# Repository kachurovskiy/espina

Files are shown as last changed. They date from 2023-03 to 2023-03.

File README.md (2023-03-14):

This project is provided "as is", without warranty of any kind ([see license](LICENSE)).

# espina

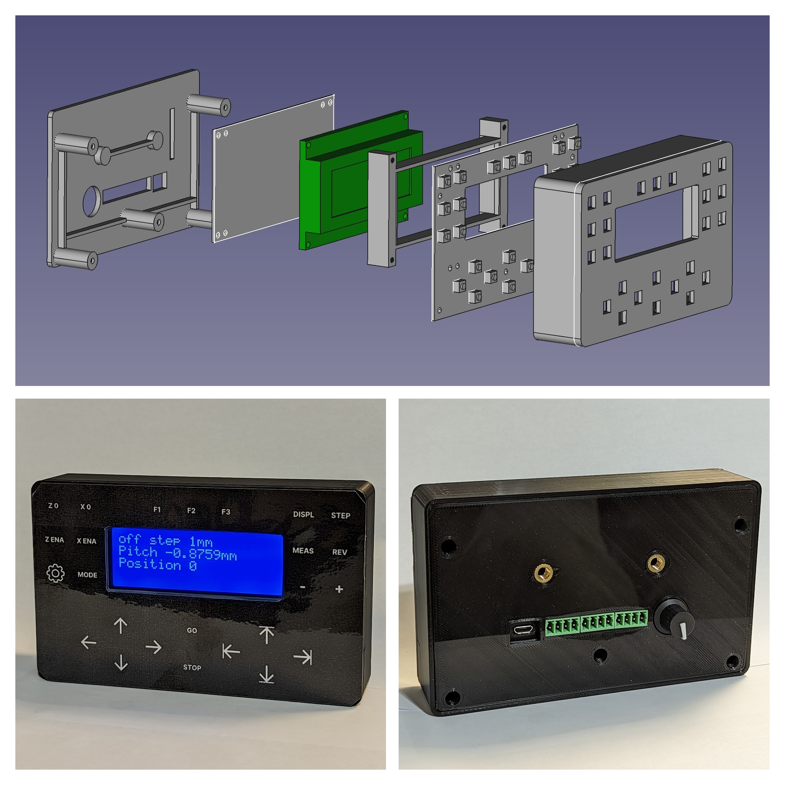
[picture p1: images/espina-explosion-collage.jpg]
Collage


ESP32 controller (PCBs, screen, case) with 1 encoder and 2 steppers. It can be used to control machinery e.g. a metal lathe or a gear cutter. Device can easily be programmed with Arduino or similar IDEs via a USB port.

# Parts

- 2x custom PCBs
- LCD 2004 standard 4-line screen
- [12-pin same-side 1mm pitch FFC connector 5cm](https://www.lcsc.com/product-detail/_JUSHUO-_C2857580.html)
- 4x 3D-printed plastic parts
- 13x M3 bolts
- Optionally, 2x M5 threaded inserts for mounting

# Schematic

espina schematic

# Printed circuit boards

Schematics and PCB layout can be viewed and edited using EasyEDA by copying [projects from `easyeda` folder](https://github.com/kachurovskiy/espina/tree/main/easyeda) to your local computer and opening them in the editor.

Gerber, BOM and pick-and-place files can be found in the [`gerber` folder](https://github.com/kachurovskiy/espina/tree/main/gerber). Smallest production run of these boards on JLCPCB would cost [$200 for 5 boards each](https://user-images.githubusercontent.com/517919/224640478-c27c72a2-1f7f-4686-9f80-fe1553a87b9b.png).

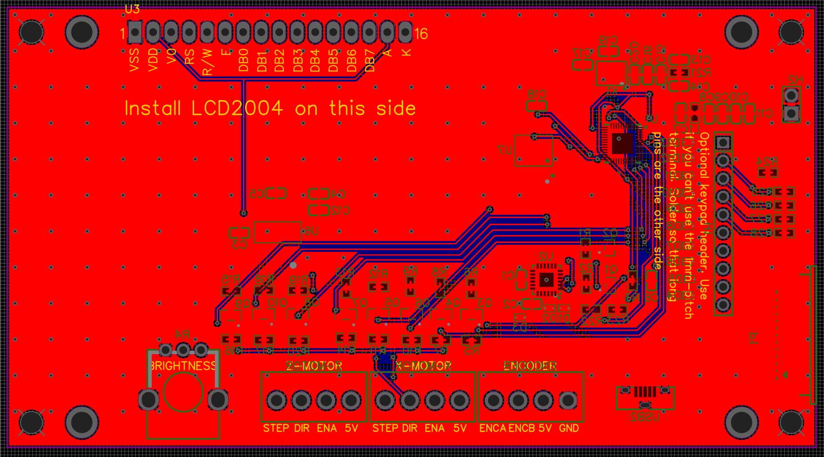
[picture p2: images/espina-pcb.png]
PCB


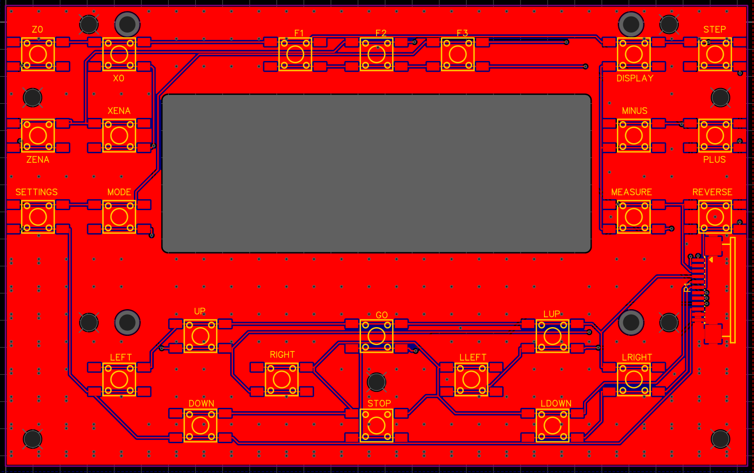
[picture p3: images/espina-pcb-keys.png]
PCB keys


Note: when ordering, JLCPCB sometimes doesn't recognize the FFC terminal part. Use the "Find part" feature, find and select [C14431](https://www.lcsc.com/product-detail/FFC-FPC-Connectors_JUSHUO-AFA07-S12FCC-00_C14431.html). Also, exclude the 2.54 headers from PCBA since you probably don't need them.

# Case

Case is designed to be 3D-printed and [consists of 4 parts](case). It assembles together with 12 M3 bolts, each 5mm long. Galvanized steel bolts are ideal since printed threads are usually too tight for nylon bolts. FreeCAD source file is also provided so it's easy to change models.

# Front panel

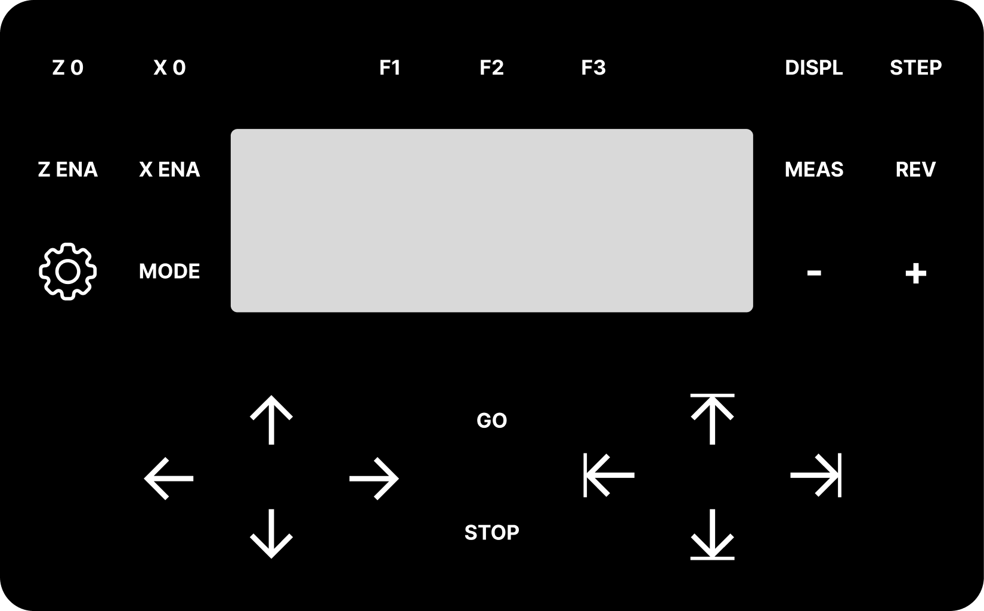
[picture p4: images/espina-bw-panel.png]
Panel Figma


Front panel can be printed on a regular printer from [this PDF](images/espina-bw-panel.pdf) with 90% scale, window cut out with a knife and then laminated. [Medium thickness double-sided tape is applied](https://i.imgur.com/JJHeC12.jpg) on the case around buttons and front panel is glued to it.

If you want to design your own panel, you can start by editing [this file](images/espina-bw-panel.fig) on [figma.com](https://www.figma.com/) for free.

# Software

One sample program for this controller is a single-axis electronic lead screw for a metal lathe, see [espinaels](https://github.com/kachurovskiy/espina/tree/main/espinaels) folder.

# Project status

This project "archived" - I decided to completely re-design it so making this historical version available for free. Drawbacks of the current design are suboptimal LCD viewing angles, older ESP32 version, lack of ESD protection, only 2 axes, old-style USB port. This version of the ELS software might not be developed much further.

# Contributions

Please report any bugs or problems. For changes and improvements, consider forking the repository and developing in parallel.

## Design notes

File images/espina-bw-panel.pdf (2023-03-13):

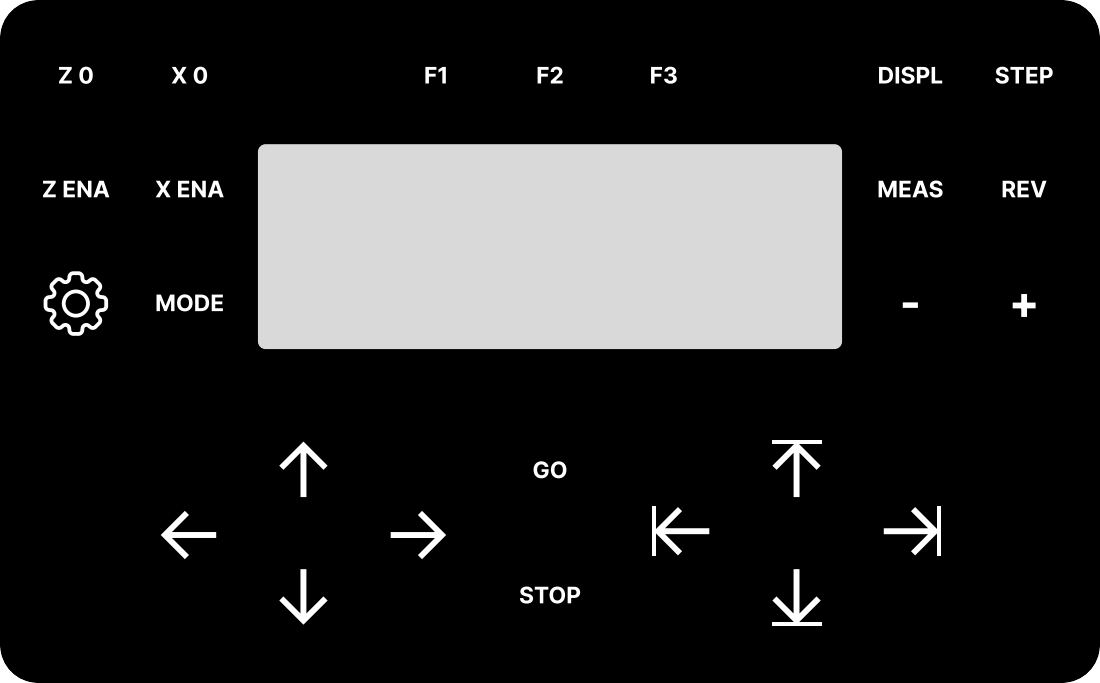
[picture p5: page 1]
STOP; DISPL; MODE; STEP; MEAS; REV; Z ENA; X ENA

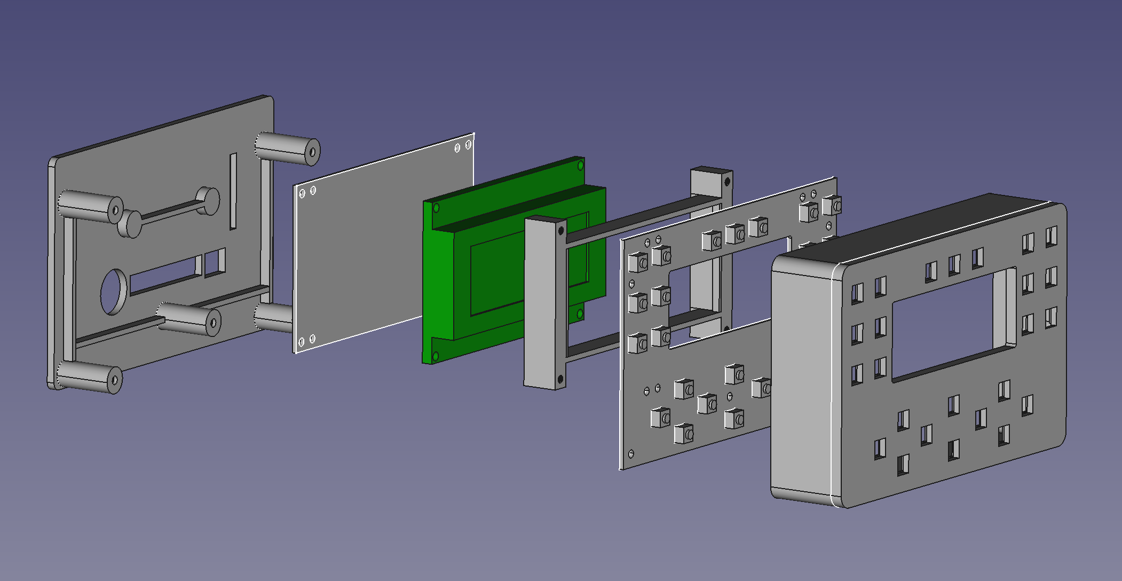
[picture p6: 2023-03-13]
images/espina-explosion.png

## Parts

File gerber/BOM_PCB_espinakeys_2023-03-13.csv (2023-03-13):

ID | Name | Designator | Footprint | Quantity | Manufacturer Part | Manufacturer | Supplier | Supplier Part | Price | Pins | 3DModel | Contributor | link
1 | KH-6X6X5H-STM | DISPLAY,DOWN,F1,F2,F3,GO,LDOWN,LEFT,LLEFT,LRIGHT,LUP,MEASURE,MINUS,MODE,PLUS,REVERSE,RIGHT,SETTINGS,STEP,STOP,UP,X0,XENA,Z0,ZENA | SW-SMD_4P-L6.0-W6.0-P4.50-LS9.0-2 | 25 | KH-6X6X5H-STM | kinghelm(金航标) | LCSC | C2837531 | 0.003 | 4 | SW-SMD_4P-L6.0-W6.0-P4.50-LS11.0 | LCSC | https://so.szlcsc.com/global.html?c=&k=C620319
2 | FPCConnector Pull type 12PIN 1MM Under the next | P1 | FPC-SMD_AFA07-S12FCC-00 | 1 | AFA07-S12FCC-00 | JS(钜硕电子) | LCSC | C14431 | 0.015 | 14 | FPC-SMD_L19.0-W6.9-H2.5-AFA07-S12FCC-00 | 立创EDA官方封装库 | https://item.szlcsc.com/15091.html

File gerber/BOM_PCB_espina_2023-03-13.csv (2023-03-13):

ID | Name | Designator | Footprint | Quantity | Manufacturer Part | Manufacturer | Supplier | Supplier Part | Price | Pins | 3DModel | Contributor | Frequency | Resistance | Resistance (Ohms) | link
1 | LCD2004 | U3 | LCD2004-PHT | 1 |  |  |  |  |  | 20 |  | Tomaž Dežman
2 | DB2EVC-3.5-4P-GN | ENCODER,X-MOTOR,Z-MOTOR | CONN-TH_4P-P3.50_DB2EVC-3.5-4P-GN | 3 | DB2EVC-3.5-4P-GN | DIBO(地博电气) | LCSC | C430552 | 0.016 | 4 | CONN-TH_4P-P3.50_DB2EVC-3.5-4P-GN | LCSC |  |  |  | https://item.szlcsc.com/426197.html
3 | KH-2.54PH180-1X2P-L11.5 | H2 | HDR-TH_2P-P2.54-V-M | 1 | KH-2.54PH180-1X2P-L11.5 | kinghelm(金航标) | LCSC | C2905434 | 0.003 | 2 | HDR2.54-M-LI-1X2P | LCSC |  |  |  | https://lcsc.com/product-detail/Pin-Header-Female-Header_Made-in-China-Made-in-China-2-54mm-1-2P_C36717.html
4 | SI2302ADS-T1 | Q7,Q6,Q4,Q3,Q5,Q8,Q9,Q10 | SOT-23-3_L2.9-W1.3-P1.90-LS2.4-BR | 8 | SI2302ADS-T1-VB | VBsemi(微碧) | LCSC | C725156 | 0.012 | 3 | SOT-23-3P_L2.9-W1.3-H1.0-LS2.4-P0.95 | LCSC |  |  |  | https://www.diodes.com/assets/Package-Files/SOT23.pdf
5 | 2kΩ | R7,R8,R6,R5,R13,R14,R10,R9,R11,R12,R15,R16,R17,R18,R19,R20,R24,R25,R26,R27,R28 | R0603 | 21 | RMC06032K1%N | Tyohm(幸亚电阻) | LCSC | C269421 | 0.001 | 2 | R0603_L1.6-W0.8-H0.8 | LCSC |  |  | 2K | https://www.mouser.in/datasheet/2/447/PYu_RT_1_to_0_01_RoHS_L_11-1669912.pdf
6 | KH-2.54PH180-1X10P-L11.5 | H1 | HDR-TH_10P-P2.54-V-M | 1 | KH-2.54PH180-1X10P-L11.5 | kinghelm(金航标) | LCSC | C2905488 | 0.015 | 10 | HDR2.54-M-LI-1X10P | LCSC |  |  |  | https://item.szlcsc.com/502965.html
7 | 100nF | C2,C5,C7,C17,C12,C8 | C0603 | 6 | C0603C104J5RAC | KEMET | LCSC | C490602 | 0.002 | 2 | C0603_L1.6-W0.8-H0.8 | LCSC |  |  |  | https://item.szlcsc.com/362304.html
8 | S9013W | Q1,Q2 | SOT-323-3_L2.0-W1.3-P1.30-LS2.1-BR | 2 | S9013W | CJ(江苏长电/长晶) | LCSC | C37634 | 0.005 | 3 | SOT-323-3_L2.0-W1.3-H1.0-LS2.1-P1.30 | lcsc |  |  |  | https://item.szlcsc.com/76687.html
9 | AMS1117-3.3 | U6 | SOT-223-3_L6.4-W3.5-P2.30-LS7.0-BR | 1 | AMS1117-3.3 | 国芯佳品 | LCSC | C2992570 | 0.008 | 4 | SOT-223-3_L6.4-W3.5-P2.30-LS7.0-BR | lcsc |  |  |  | https://atta.szlcsc.comnull
10 | ULC0511CDN | D1,D2,D3,D4,D5,D6,D7,D8,D9,D10,D11,D12,D13 | X1-DFN1006-2_L1.0-W0.6-RD | 13 | ULC0511CDN | Leiditech(雷卯电子) | LCSC | C384841 | 0.008 | 2 | DFN1006_L1.0-W0.6-H0.5 | LCSC |  |  |  | https://item.szlcsc.com/162710.html
11 | 40MHz | X1 | OSC-SMD_4P-L3.2-W2.5-BL_SIT8008BI | 1 | X322540MPB4SI | YXC(扬兴晶振) | LCSC | C9010 | 0.015 | 4 | OSC-SMD_4P-L3.2-W2.5-H1.0 | lcsc |  |  |  | https://item.szlcsc.com/264073.html
12 | 10nF | C13 | C0603 | 1 | CC0603KRX7R9BB103 | YAGEO(国巨) | LCSC | C100042 |  | 2 | C0603_L1.6-W0.8-H0.8 | lcsc |  |  |  | https://item.szlcsc.com/362304.html
13 | 3.3nF | C14 | C0603 | 1 | CC0603KRX7R7BB332 | YAGEO | LCSC | C519418 | 0.001 | 2 | C0603_L1.6-W0.8-H0.8 | LCSC |  |  |  | https://item.szlcsc.com/362304.html
14 | 100pF | C15 | C0603 | 1 | CC0603KRX7R9BB101 | YAGEO(国巨) | LCSC | C160903 |  | 2 | C0603_L1.6-W0.8-H0.8 | LCSC |  |  |  | https://item.szlcsc.com/362304.html
15 | 2nH | L1 | L0603 | 1 | SDCL1608C2N0STDF | Sunlord | LCSC | C370234 | 0.001 | 2 | L0603_L1.6-W0.8-H0.5_BEAD | LCSC |  |  |  | https://item.szlcsc.com/344093.html
16 | 20K | R21 | R0603 | 1 | AC0603FR-0720KL | YAGEO(国巨) | LCSC | C125934 |  | 2 | R0603_L1.6-W0.8-H0.8 | lcsc |  | 20kΩ |  | https://www.mouser.in/datasheet/2/447/PYu_RT_1_to_0_01_RoHS_L_11-1669912.pdf
17 | ESP32-D0WD | U1 | QFN-48_L5.0-W5.0-P0.35-BL-EP3.7 | 1 | ESP32-D0WD | ESPRESSIF(乐鑫) | LCSC | C130167 | 0.344 | 49 | QFN-48_L5.0-W5.0-H0.9-P0.35-BL-EP3.7 | LCSC | - |  |  | https://item.szlcsc.com/479661.html
18 | W25Q32JVSSIQ | U7 | SOIC-8_L5.3-W5.3-P1.27-LS8.0-BL | 1 | W25Q32JVSSIQ | WINBOND(华邦) | LCSC | C179173 | 0.052 | 8 | SOIC-8_L5.3-W5.3-H1.9-LS7.9-P1.27 | LCSC |  |  |  | https://item.szlcsc.com/63461.html
19 | 1uF | C1,C6,C10,C16,C18 | C0603 | 5 | 0603B105K160AT | FH(风华) | LCSC | C111770 | 0.002 | 2 | C0603_L1.6-W0.8-H0.8 | lcsc |  |  |  | https://item.szlcsc.com/362304.html
20 | 10uF | C3,C4,C9,C11 | C0603 | 4 | 0603X106K160NT | FH(风华) | LCSC | C70225 | 0.007 | 2 | C0603_L1.6-W0.8-H0.8 | lcsc |  |  |  | https://item.szlcsc.com/362304.html
21 | 15pF | C19,C20 | C0603 | 2 | CC0603JRNPO9BN150 | YAGEO(国巨) | LCSC | C107037 |  | 2 | C0603_L1.6-W0.8-H0.8 | lcsc |  |  |  | https://item.szlcsc.com/362304.html
22 | 10kΩ | R1,R2,R3 | R0603 | 3 | RMC060310KFN | Tyohm(幸亚电阻) | LCSC | C269701 | 0.001 | 2 | R0603_L1.6-W0.8-H0.8 | LCSC |  |  | 10K | https://www.mouser.in/datasheet/2/447/PYu_RT_1_to_0_01_RoHS_L_11-1669912.pdf
23 | 470 | R22,R23 | R0603 | 2 | RC0603JR-07470RL | YAGEO(国巨) | LCSC | C114433 |  | 2 | R0603_L1.6-W0.8-H0.8 | lcsc |  | 470Ω |  | https://www.mouser.in/datasheet/2/447/PYu_RT_1_to_0_01_RoHS_L_11-1669912.pdf
24 | CH9102F | U2 | QFN-24_L4.0-W4.0-P0.50-BL-EP2.5 | 1 | CH9102F | WCH(南京沁恒) | LCSC | C2858418 | 0.221 | 25 | QFN-24_L4.0-W4.0-P0.50-BL-EP2.5 | LCSC |  |  |  | http://ww1.microchip.com/downloads/en/DeviceDoc/00002165B.pdf
25 | 10kΩ | R4 | RES-ADJ-TH_RK09K1130AJ3 | 1 | RK09K1130AJ3 | ALPSALPINE(阿尔卑斯阿尔派) | LCSC | C388854 | 0.099 | 5 | RES-ADJ-TH_RK09K1130AJ3 | LCSC |  |  |  | https://lcsc.com/product-detail/New-Arrivals_ALPS-Electric-RK09K1130AJ3_C388854.html
26 | 1051330011 | USB2 | MICRO-USB-SMD_1051330011 | 1 | 1051330011 | MOLEX | LCSC | C586226 | 0.069 | 8 | MICRO-USB-SMD_1051330011 | LCSC |  |  |  | https://item.szlcsc.com/614076.html?ref=editor&logined=true
27 | FPCConnector Pull type 12PIN 1MM Under the next | P1 | FPC-SMD_AFA07-S12FCC-00 | 1 | AFA07-S12FCC-00 | JS(钜硕电子) | LCSC | C14431 | 0.015 | 14 | FPC-SMD_L19.0-W6.9-H2.5-AFA07-S12FCC-00 | 立创EDA官方封装库 |  |  |  | https://item.szlcsc.com/15091.html

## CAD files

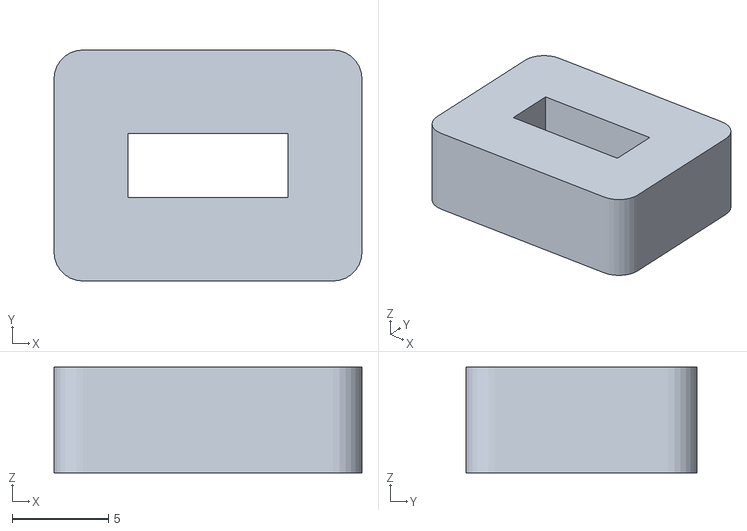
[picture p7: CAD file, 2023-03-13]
case/espina-USB collar.stl
16.0 x 12.0 x 5.50

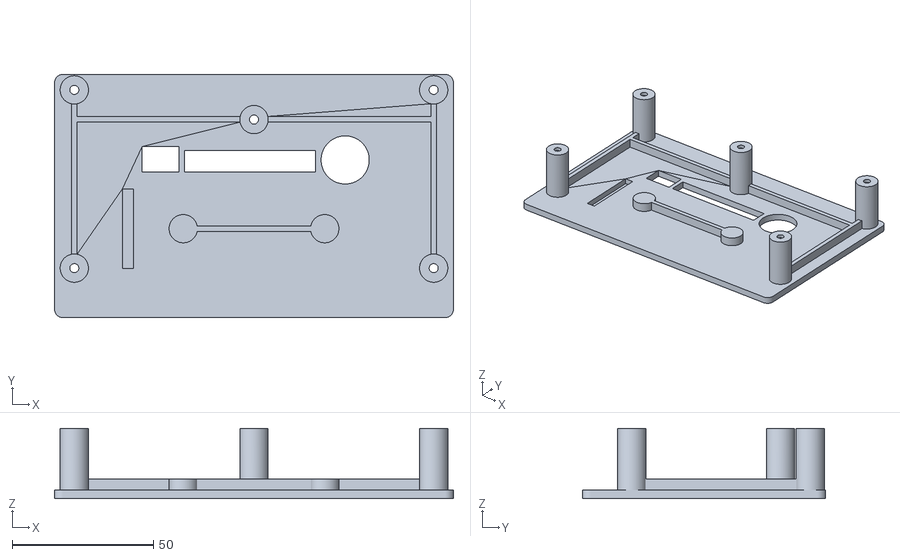
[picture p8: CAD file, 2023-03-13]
case/espina-Back.stl
141.0 x 86.0 x 24.9

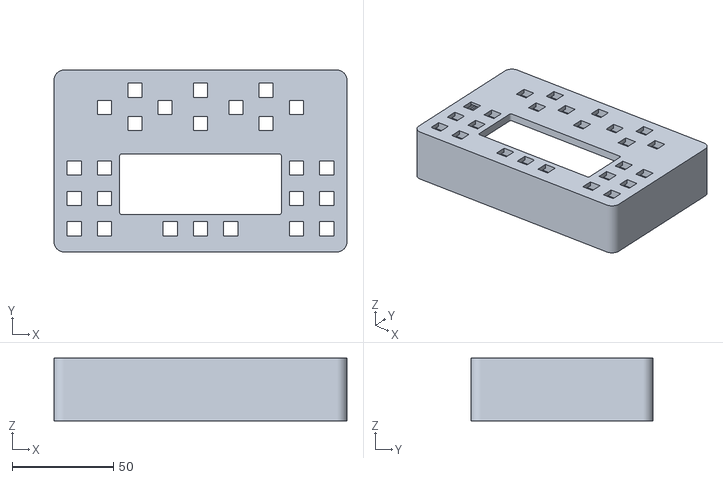
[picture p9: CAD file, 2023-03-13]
case/espina-Case.stl
145.0 x 90.0 x 31.0

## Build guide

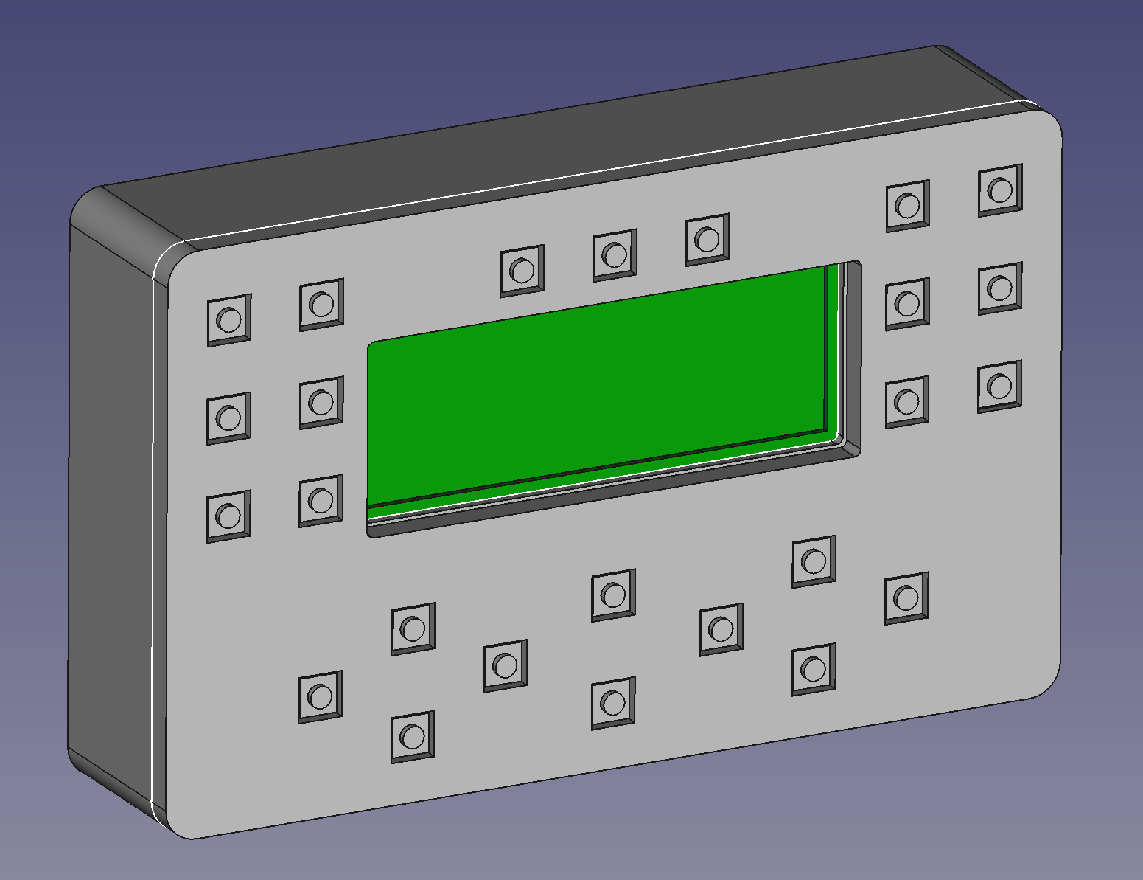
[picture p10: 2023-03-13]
images/espina-assembled.png

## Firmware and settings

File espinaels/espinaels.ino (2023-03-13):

// https://github.com/kachurovskiy/espina

/* Change values in this section to suit your hardware. */

// Define your hardware parameters here. Don't remove the ".0" at the end.
#define ENCODER_STEPS 600.0 // 600 step spindle optical rotary encoder
#define MOTOR_STEPS 200.0
#define LEAD_SCREW_DU 20000.0 // 2mm lead screw in deci-microns (10^-7) of a meter

// Spindle rotary encoder pins. Swap values if the rotation direction is wrong.
#define ENC_A 36
#define ENC_B 39

// Stepper pulse and acceleration constants.
#define PULSE_MIN_US round(500.0 * 200.0 / MOTOR_STEPS) // Microseconds to wait after high pulse, min.
#define PULSE_MAX_US round(2000.0 * 200.0 / MOTOR_STEPS) // Microseconds to wait after high pulse, max. Slow start.
#define ACCELERATION 20
#define INVERT_STEPPER false // change (true/false) if the carriage moves e.g. "left" when you press "right".
#define DISABLE_STEPPER_WHEN_RESTING false

/* Changing anything below shouldn't be needed for basic use. */

#define LONG_MIN long(-2147483648)
#define LONG_MAX long(2147483647)

#define LOOP_COUNTER_MAX 1500 // 1500 loops without stepper move to start reading buttons
#define DUPR_MAX long(100000) // 10mm
#define STARTS_MAX 124 // No more than 124-start thread

// Ratios between spindle and stepper.
#define ENCODER_TO_STEPPER_STEP_RATIO MOTOR_STEPS / (LEAD_SCREW_DU * ENCODER_STEPS)
#define STEPPER_TO_ENCODER_STEP_RATIO LEAD_SCREW_DU * ENCODER_STEPS / MOTOR_STEPS

// If time between encoder ticks is less than this, direction change is not allowed.
// Effectively this limits direction change to the time when spindle is <20rpm.
#define DIR_CHANGE_DIFF_MICROS (int) (5000 * ENCODER_STEPS / 600)

// Version of the EEPROM storage format, should be changed when non-backward-compatible
// changes are made to the storage logic, resulting in EEPROM wipe on first start.
#define EEPROM_VERSION 1

// To be incremented whenever a measurable improvement is made.
#define SOFTWARE_VERSION 1

// To be changed whenever a different PCB / encoder / stepper / ... design is used.
#define HARDWARE_VERSION 1

#define Z_DIR 16
#define Z_STEP 17
#define Z_ENA 4

#define X_DIR 26
#define X_STEP 25
#define X_ENA 27

// Keypad columns left-to-right
#define KP_1 34 // input only, no pull-up/down
#define KP_2 35 // input only, no pull-up/down
#define KP_3 32
#define KP_4 33
#define KP_5 14

// Keypad rows bottom-to-top
#define KP_6 12
#define KP_7 13
#define KP_8 15
#define KP_9 2
#define KP_10 0

// Code for each button calculated as row*100+column
#define B_LEFT  33
#define B_RIGHT 214
#define B_MINUS 1332
#define B_PLUS 1232
#define B_ON 1533
#define B_OFF 1514
#define B_STOPL 1314
#define B_STOPR 1233
#define B_DISPL 1334
#define B_STEP 1234
#define B_MODE 232
#define B_MEASURE 1335
#define B_REVERSE 1235

#define ADDR_EEPROM_VERSION 0 // takes 1 byte
#define ADDR_ONOFF 1 // takes 1 byte
#define ADDR_DUPR 2 // takes 4 bytes
#define ADDR_POS 6 // takes 4 bytes
#define ADDR_LEFT_STOP 10 // takes 4 bytes
#define ADDR_RIGHT_STOP 14 // takes 4 bytes
#define ADDR_SPINDLE_POS 18 // takes 4 bytes
#define ADDR_OUT_OF_SYNC 22 // takes 2 bytes
#define ADDR_SHOW_ANGLE 24 // takes 1 byte
#define ADDR_SHOW_TACHO 25 // takes 1 byte
#define ADDR_MOVE_STEP 26 // takes 2 bytes
#define ADDR_STARTS 28 // takes 2 bytes
#define ADDR_MODE 30 // takes 2 bytes
#define ADDR_MEASURE 32 // takes 2 bytes

#define MOVE_STEP_1 10000 // 1mm
#define MOVE_STEP_2 1000 // 0.1mm
#define MOVE_STEP_3 100 // 0.01mm
#define MOVE_STEP_4 10 // 1 micron
#define MOVE_STEP_IMP_1 25400 // 1/10"
#define MOVE_STEP_IMP_2 2540 // 1/100"
#define MOVE_STEP_IMP_3 254 // 1/1000" also known as 1 thou

#define MODE_NORMAL 0
#define MODE_MULTISTART 1
#define MODE_ASYNC 2

#define MEASURE_METRIC 0
#define MEASURE_INCH 1
#define MEASURE_TPI 2

// For MEASURE_TPI, round TPI to the nearest integer if it's within this range of it.
// E.g. 80.02tpi would be shown as 80tpi but 80.04tpi would be shown as-is.
#define TPI_ROUND_EPSILON 0.03

#define RPM_BULK ENCODER_STEPS // Measure RPM averaged over this number of encoder pulses
#define RPM_UPDATE_INTERVAL_MICROS 1000000 // Don't redraw RPM more often than once per second

// Uncomment to print out debug info in Serial.
// #define DEBUG

#define DREAD(x) digitalRead(x)
#define DHIGH(x) digitalWrite(x, HIGH)
#define DLOW(x) digitalWrite(x, LOW)

#include <SPI.h>
#include <Wire.h>
#include <LiquidCrystal.h>
LiquidCrystal lcd(5, 18, 23, 19, 22, 21);
long lcdHash = 0;

#include <EEPROM.h>

unsigned long buttonDownTime = 0;
unsigned long buttonUpTime = 0;
int buttonId = 0;
volatile long loopCounter = 0;
int buttonLoopCounter = 0;
bool isOn = false;
unsigned long resetMillis = 0;
bool resetOnStartup = false;

volatile long dupr = 0; // pitch, tenth of a micron per rotation
long savedDupr = 0; // dupr saved in EEPROM
long duprPrevious = 0;

int starts = 1; // number of starts in a multi-start thread
int savedStarts = 0; // starts saved in EEPROM

volatile long pos = 0; // relative position of the stepper motor, in steps
long savedPos = 0; // value saved in EEPROM
float fractionalPos = 0.0; // fractional distance in steps that we meant to travel but couldn't

volatile long leftStop = 0; // left stop value of pos
long savedLeftStop = 0; // value saved in EEPROM
bool leftStopFlag = true; // prevent toggling the stop while button is pressed.

volatile long rightStop = 0; // right stop value of pos
long savedRightStop = 0; // value saved in EEPROM
bool rightStopFlag = true; // prevent toggling the stop while button is pressed.

volatile unsigned long spindleEncTime = 0; // micros() of the previous spindle update
volatile unsigned long spindleEncTimeDiff = 0; // micros() since the previous spindle update
volatile unsigned long spindleEncTimeDiffBulk = 0; // micros() between RPM_BULK spindle updates
volatile unsigned long spindleEncTimeAtIndex0 = 0; // micros() when spindleEncTimeIndex was 0
volatile int spindleEncTimeIndex = 0; // counter going between 0 and RPM_BULK - 1
volatile int spindleDeltaPrev = 0; // Previously detected spindle direction
volatile long spindlePos = 0; // Spindle position
long savedSpindlePos = 0; // spindlePos value saved in EEPROM
long spindleLeftStop = 0;
long spindleRightStop = 0;

volatile int spindlePosSync = 0;
int savedSpindlePosSync = 0;

volatile int stepDelayUs = PULSE_MAX_US;
volatile bool stepDelayDirection = true; // To reset stepDelayUs when direction changes.
volatile bool stepDirectionInitialized = false;
volatile unsigned long stepStartMicros = 0;
int stepperEnableCounter = 0;

bool showAngle = false; // Whether to show 0-359 spindle angle on screen
bool showTacho = false; // Whether to show spindle RPM on screen
bool savedShowAngle = false; // showAngle value saved in EEPROM
bool savedShowTacho = false; // showTacho value saved in EEPROM
int shownRpm = 0;
unsigned long shownRpmTime = 0; // micros() when shownRpm was set

int moveStep = 0; // thousandth of a mm
int savedMoveStep = 0; // moveStep saved in EEPROM
volatile bool movingManually = false; // whether stepper is being moved by left/right buttons

volatile int mode = -1; // mode of operation (ELS, multi-start ELS, asynchronous)
int savedMode = -1; // mode saved in EEPROM

int measure = MEASURE_METRIC; // Whether to show distances in inches
int savedMeasure = MEASURE_METRIC; // measure value saved in EEPROM

int getApproxRpm() {
  if (!showTacho) {
    return 0;
  }
  unsigned long t = micros();
  if (t > spindleEncTime + 100000) {
    // RPM less than 10.
    return 0;
  }
  if (t < shownRpmTime + RPM_UPDATE_INTERVAL_MICROS) {
    // Don't update RPM too often to avoid flickering.
    return shownRpm;
  }
  int rpm = 0;
  if (spindleEncTimeDiffBulk > 0) {
    rpm = 60000000 / spindleEncTimeDiffBulk;
    if (abs(rpm - shownRpm) < (rpm < 1000 ? 2 : 5)) {
      // Don't update RPM with insignificant differences.
      rpm = shownRpm;
    }
  }
  return rpm;
}

bool stepperIsRunning() {
  return micros() - stepStartMicros < 10000;
}

void printMicrons(long deciMicrons) {
  if (deciMicrons == 0) {
    lcd.print("0");
    return;
  }
  bool imperial = measure != MEASURE_METRIC;
  long v = imperial ? round(deciMicrons / 25.4) : deciMicrons;
  int points = 0;
  if (v == 0) {
    points = 5;
  } else if ((v % 10) != 0) {
    points = 4;
  } else if ((v % 100) != 0) {
    points = 3;
  } else if ((v % 1000) != 0) {
    points = 2;
  } else if ((v % 10000) != 0) {
    points = 1;
  }
  lcd.print(deciMicrons / (imperial ? 254000.0 : 10000.0), points);
  lcd.print(imperial ? "\"" : "mm");
}

void updateDisplay(bool beforeRunning) {
  int rpm = getApproxRpm();
  // Hide rows 3 and 4 if ON and about to or is already moving.
  // Not hiding when off since it results in flickering of rows 3 and 4 during short manual moves.
  bool running = isOn && (beforeRunning || stepperIsRunning());
  // Sum of values affecting rows 1 and 2 of the LCD.
  long hashRows12 = dupr + isOn * 2 + leftStop / 3
                    + rightStop / 4 + spindlePosSync * 5 + resetOnStartup * 6
                    + moveStep * 7 + running * 8 + starts * 12 + mode * 13 + measure * 14;
  // Sum of values affecting rows 3 and 4 of the LCD.
  long hashRows34 = pos * 9 + showAngle * 10 + (showTacho ? rpm : -1) * 11 + measure * 14;
  // Ignore changes in hashRows34 when stepper is running since they aren't shown.
  long newLcdHash = hashRows12 + (running ? 0 : hashRows34);
  // Don't show angle if stepper is running or spindle is turning.
  bool spindleStopped = micros() > spindleEncTime + 100000;
  if (!running && showAngle && spindleStopped) {
    newLcdHash += spindlePos;
  }

  // Don't spend 40ms and flicker the screen if nothing changed.
  if (newLcdHash == lcdHash) {
    return;
  }

  lcdHash = newLcdHash;
  lcd.clear();

  // First row.
  lcd.setCursor(0, 0);
  if (mode == MODE_MULTISTART) {
    lcd.print("MUL ");
  } else if (mode == MODE_ASYNC) {
    lcd.print("ASY ");
  }
  lcd.print(isOn ? "ON" : "off");
  if (leftStop != LONG_MAX && rightStop != LONG_MIN) {
    lcd.print(" LR");
  } else if (leftStop != LONG_MAX) {
    lcd.print(" L");
  } else if (rightStop != LONG_MIN) {
    lcd.print("  R");
  }

  if (spindlePosSync) {
    lcd.print(" SYN");
  }
  if (resetOnStartup) {
    lcd.print(" LTW");
  }
  if (mode == MODE_NORMAL && !resetOnStartup && !spindlePosSync) {
    lcd.print(" step ");
  } else {
    lcd.print(" ");
  }
  printMicrons(moveStep);

  // Second row.
  lcd.setCursor(0, 1);
  lcd.print("Pitch ");
  if (measure != MEASURE_TPI) {
    printMicrons(dupr);
  } else {
    float tpi = 254000.0 / dupr;
    if (abs(tpi - round(tpi)) < TPI_ROUND_EPSILON) {
      lcd.print(round(tpi));
    } else {
      int tpi100 = round(tpi * 100);
      int points = 0;
      if ((tpi100 % 10) != 0) {
        points = 2;
      } else if ((tpi100 % 100) != 0) {
        points = 1;
      }
      lcd.print(tpi, points);
    }
    lcd.print("tpi");
  }
  if (starts != 1) {
    lcd.print(" x");
    lcd.print(starts);
  }

  if (running) {
    // Stepper is running, updateDisplay() will no longer be called soon,
    // don't draw position, RPM and angle that won't be accurate shortly.
    return;
  }

  // Third row.
  lcd.setCursor(0, 2);
  lcd.print("Position ");
  printMicrons(round(pos * LEAD_SCREW_DU / MOTOR_STEPS));

  // Fourth row.
  lcd.setCursor(0, 3);
  if (showAngle) {
    lcd.print("Angle ");
    if (spindleStopped) {
      lcd.print(((spindlePos % (int) ENCODER_STEPS + (int) ENCODER_STEPS) % (int) ENCODER_STEPS) * 360 / ENCODER_STEPS, 2);
      lcd.print(char(223));
    }
  } else if (showTacho) {
    lcd.print("Tacho ");
    lcd.print(rpm);
    if (shownRpm != rpm) {
      shownRpm = rpm;
      shownRpmTime = micros();
    }
    lcd.print("rpm");
  }
}

void saveInt(int i, int v) {
  // Can't concatenate all in one line due to compiler problems, same throughout the code.
#ifdef DEBUG
  Serial.print("Saving int at ");
  Serial.print(i);
  Serial.print(" = ");
  Serial.println(v);
#endif
  EEPROM.write(i, v >> 8 & 0xFF);
  EEPROM.write(i + 1, v & 0xFF);
}
int loadInt(int i) {
  // 255 is the default value when nothing was written before.
  if (EEPROM.read(i) == 255 && EEPROM.read(i + 1) == 255) {
    return 0;
  }
  return (EEPROM.read(i) << 8) + EEPROM.read(i + 1);
}
void saveLong(int i, long v) {
#ifdef DEBUG
  Serial.print("Saving long at ");
  Serial.print(i);
  Serial.print(" = ");
  Serial.println(v);
#endif
  EEPROM.write(i, v >> 24 & 0xFF);
  EEPROM.write(i + 1, v >> 16 & 0xFF);
  EEPROM.write(i + 2, v >> 8 & 0xFF);
  EEPROM.write(i + 3, v & 0xFF);
}
long loadLong(int i) {
  long p0 = EEPROM.read(i);
  long p1 = EEPROM.read(i + 1);
  long p2 = EEPROM.read(i + 2);
  long p3 = EEPROM.read(i + 3);
  // 255 is the default value when nothing was written before.
  if (p0 == 255 && p1 == 255 && p2 == 255 && p3 == 255) {
    return 0;
  }
  return (p0 << 24) + (p1 << 16) + (p2 << 8) + p3;
}

// Called on a FALLING interrupt for the spindle rotary encoder pin.
// Keeps track of the spindle position.
void spinEnc() {
  unsigned long microsNow = micros();
  if (spindleEncTimeIndex == 0) {
    spindleEncTimeDiffBulk = microsNow - spindleEncTimeAtIndex0;
    spindleEncTimeAtIndex0 = microsNow;
  }
  spindleEncTimeIndex = (spindleEncTimeIndex + 1) % int(RPM_BULK);

  int delta;
  spindleEncTimeDiff = microsNow - spindleEncTime;
  if (spindleEncTimeDiff > DIR_CHANGE_DIFF_MICROS || !stepDirectionInitialized) {
    delta = DREAD(ENC_B) ? -1 : 1;
    spindleDeltaPrev = delta;
  } else {
    // Spindle is going fast, unlikely to change direction momentarily.
    delta = spindleDeltaPrev;
  }
  spindlePos += delta;
  spindleEncTime = microsNow;

  if (spindlePosSync != 0) {
    spindlePosSync += delta;
    if (spindlePosSync == 0 || spindlePosSync == ENCODER_STEPS) {
      spindlePosSync = 0;
      spindlePos = spindleFromPos(pos);
    }
  }
}

void setup() 
{
  pinMode(ENC_A, INPUT_PULLUP);
  pinMode(ENC_B, INPUT_PULLUP);

  pinMode(Z_DIR, OUTPUT);
  pinMode(Z_STEP, OUTPUT);
  pinMode(Z_ENA, OUTPUT);
  DHIGH(Z_STEP);

  pinMode(X_DIR, OUTPUT);
  pinMode(X_STEP, OUTPUT);
  pinMode(X_ENA, OUTPUT);
  DHIGH(X_STEP);

  EEPROM.begin(256);
  // Wipe EEPROM if this is the first start after uploading a new build.
  if (EEPROM.read(ADDR_EEPROM_VERSION) != EEPROM_VERSION) {
    for (int i = 0; i < 256; i++) {
      EEPROM.write(i, 255); // 255 is the default value.
    }
    EEPROM.write(ADDR_EEPROM_VERSION, EEPROM_VERSION);
    saveLong(ADDR_LEFT_STOP, savedLeftStop = leftStop = LONG_MAX);
    saveLong(ADDR_RIGHT_STOP, savedRightStop = rightStop = LONG_MIN);
    saveInt(ADDR_MOVE_STEP, MOVE_STEP_1);
  }

  isOn = EEPROM.read(ADDR_ONOFF) == 1;
  savedDupr = dupr = loadLong(ADDR_DUPR);
  savedStarts = starts = min(STARTS_MAX, max(1, loadInt(ADDR_STARTS)));
  savedPos = pos = loadLong(ADDR_POS);
  savedLeftStop = leftStop = loadLong(ADDR_LEFT_STOP);
  savedRightStop = rightStop = loadLong(ADDR_RIGHT_STOP);
  savedSpindlePos = spindlePos = loadLong(ADDR_SPINDLE_POS);
  savedSpindlePosSync = spindlePosSync = loadInt(ADDR_OUT_OF_SYNC);
  savedShowAngle = showAngle = EEPROM.read(ADDR_SHOW_ANGLE) == 1;
  savedShowTacho = showTacho = EEPROM.read(ADDR_SHOW_TACHO) == 1;
  savedMoveStep = moveStep = loadInt(ADDR_MOVE_STEP);
  savedMode = loadInt(ADDR_MODE);
  savedMeasure = measure = loadInt(ADDR_MEASURE);
  // Don't move on power-on.
  setMode((isOn && savedMode == MODE_ASYNC) ? MODE_NORMAL : savedMode);

  if (DISABLE_STEPPER_WHEN_RESTING) {
    stepperEnable(isOn);
  } else {
    DHIGH(Z_ENA);
  }

  lcd.begin(20, 4);
  updateDisplay(false /*beforeRunning*/);

  Serial.begin(9600);
  Serial.print("Espina H");
  Serial.print(HARDWARE_VERSION);
  Serial.print(" V");
  Serial.println(SOFTWARE_VERSION);

  preventMoveOnStart();

  attachInterrupt(digitalPinToInterrupt(ENC_A), spinEnc, FALLING);
  
  pinMode(KP_1, INPUT); // no built-in pull-down/up
  pinMode(KP_2, INPUT); // no built-in pull-down/up
  pinMode(KP_3, INPUT_PULLDOWN);
  pinMode(KP_4, INPUT_PULLDOWN);
  pinMode(KP_5, INPUT_PULLDOWN);
  pinMode(KP_6, OUTPUT);
  pinMode(KP_7, OUTPUT);
  pinMode(KP_8, OUTPUT);
  pinMode(KP_9, OUTPUT);
  pinMode(KP_10, OUTPUT);
}

void preventMoveOnStart() {
  // Sometimes, especially if ELS was run outside above max RPM before, pos and spindlePos
  // will be out of sync causing immediate stepper movement if isOn. This could be dangerous
  // and surely won't be expected by the operator.
  long newPos = posFromSpindle(spindlePos, true);
  if (isOn && newPos != pos) {
#ifdef DEBUG
    Serial.println("Losing the thread");
#endif
    resetOnStartup = true;
    markAsZero();
  }
}

// Saves all positions in EEPROM, should be called infrequently to reduce EEPROM wear.
void saveIfChanged() {
  bool changed = false;
  if (dupr != savedDupr) {
    saveLong(ADDR_DUPR, savedDupr = dupr);
    changed = true;
  }
  if (starts != savedStarts) {
    saveInt(ADDR_STARTS, savedStarts = starts);
    changed = true;
  }
  if (pos != savedPos) {
    saveLong(ADDR_POS, savedPos = pos);
    changed = true;
  }
  if (leftStop != savedLeftStop) {
    saveLong(ADDR_LEFT_STOP, savedLeftStop = leftStop);
    changed = true;
  }
  if (rightStop != savedRightStop) {
    saveLong(ADDR_RIGHT_STOP, savedRightStop = rightStop);
    changed = true;
  }
  if (spindlePos != savedSpindlePos) {
    saveLong(ADDR_SPINDLE_POS, savedSpindlePos = spindlePos);
    changed = true;
  }
  if (spindlePosSync != savedSpindlePosSync) {
    saveInt(ADDR_OUT_OF_SYNC, savedSpindlePosSync = spindlePosSync);
    changed = true;
  }
  if (showAngle != savedShowAngle) {
    EEPROM.write(ADDR_SHOW_ANGLE, savedShowAngle = showAngle);
    changed = true;
  }
  if (showTacho != savedShowTacho) {
    EEPROM.write(ADDR_SHOW_TACHO, savedShowTacho = showTacho);
    changed = true;
  }
  if (moveStep != savedMoveStep) {
    saveInt(ADDR_MOVE_STEP, savedMoveStep = moveStep);
    changed = true;
  }
  if (mode != savedMode) {
    saveInt(ADDR_MODE, savedMode = mode);
    changed = true;
  }
  if (measure != savedMeasure) {
    saveInt(ADDR_MEASURE, savedMeasure = measure);
    changed = true;
  }
  if (changed) {
    EEPROM.commit();
  }
}

// Checks if the button can be considered pressed.
// Protects against noise and counting presses too often.
bool checkAndMarkButtonTime(int button) {
  unsigned long m = millis();
  if (buttonId != button) {
    buttonId = button;
    buttonDownTime = m;
    // Protect from spurious presses caused by noise by requiring button to be
    // pressed for a bit before it actually triggers.
    return false;
  }
  if (m < buttonDownTime + 50) {
    // Button isn't down long enough yet.
    return false;
  }
  if (m > buttonUpTime + 300) {
    buttonUpTime = m;
    buttonDownTime = 0;
    return true;
  }
  return false;
}
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
void loop() {
  int button = getButton();
  if (button >= 0 && button != lastButton) {
    Serial.println(button);
  }
  lastButton = button;
  checkOnOffButton(button);
  checkPlusMinusButtons(button);
  checkLeftStopButton(button);
  checkRightStopButton(button);
  checkMoveButtons(button);
  checkDisplayButton(button);
  checkMoveStepButton(button);
  checkModeButton(button);
  checkMeasureButton(button);
  checkReverseButton(button);

  noInterrupts();
  long spindlePosCopy = spindlePos;
  long spindlePosSyncCopy = spindlePosSync;
  interrupts();

  // Move the stepper if needed.
  if (isOn && mode != MODE_ASYNC && spindlePosSyncCopy == 0) {
    long newPos = posFromSpindle(spindlePosCopy, true);
    if (newPos != pos) {
      // Move the stepper to the right position.
      step(newPos > pos, 1);
      if (loopCounter > 0) {
        loopCounter = 0;
      }

      // No long calls on this path or stepper will move unevenly.
      return;
    }
  }

  // Perform auxiliary logic but don't take more than a few milliseconds since
  // stepper just be moving slowly and will need signalling soon.

  // When standing at the stop, ignore full spindle turns.
  // This allows to avoid waiting when spindle direction reverses
  // and reduces the chance of the skipped stepper steps since
  // after a reverse the spindle starts slow.
  if (dupr != 0) {
    noInterrupts();
    if (rightStop != LONG_MIN && pos == rightStop) {
      long stopSpindlePos = spindleFromPos(rightStop);
      if (dupr > 0) {
        if (spindlePos < stopSpindlePos - ENCODER_STEPS) {
          spindlePos += ENCODER_STEPS;
        }
      } else {
        if (spindlePos > stopSpindlePos + ENCODER_STEPS) {
          spindlePos -= ENCODER_STEPS;
        }
      }
    } else if (leftStop != LONG_MAX && pos == leftStop) {
      long stopSpindlePos = spindleFromPos(leftStop);
      if (dupr > 0) {
        if (spindlePos > stopSpindlePos + ENCODER_STEPS) {
          spindlePos -= ENCODER_STEPS;
        }
      } else {
        if (spindlePos < stopSpindlePos - ENCODER_STEPS) {
          spindlePos += ENCODER_STEPS;
        }
      }
    }
    interrupts();
    checkIfNextStart();
  }

  loopCounter++;
  if (loopCounter > LOOP_COUNTER_MAX) {
    // Only check buttons when stepper is surely not running.
    // It might have to run any millisecond though e.g. when leaving the stop
    // so it still should complete within milliseconds.
    if (loopCounter % 8 == 0) {
      // This takes a really long time.
      updateDisplay(false /*beforeRunning*/);
    }
    if (loopCounter % 137 == 0) {
      saveIfChanged();
    }

    // Drop the lost thread warning after some time.
    if (resetOnStartup && loopCounter > 2 * LOOP_COUNTER_MAX) {
      resetOnStartup = false;
    }
  }
}

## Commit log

2023-03-13 Initial version
    [BOM_PCB_espina_2023-03-13.csv, BOM_PCB_espinakeys_2023-03-13.csv, PickAndPlace_PCB_espina_2023-03-13.csv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]
2023-03-13 Place plus and minus buttons in the bottom row according to the panel icons
2023-03-13 Remove remaning NanoEls references, reset versions
    [espinaels.ino]
2023-03-13 Link to case files
2023-03-14 Added schematic image
